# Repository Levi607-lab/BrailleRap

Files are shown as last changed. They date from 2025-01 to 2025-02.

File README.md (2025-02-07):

<figure> 
 
 # BrailleRAP
 This fork is based on the BrailleRap project: [https://github.com/braillerap/BrailleRap](https://github.com/braillerap/BrailleRap).

After building three BrailleRap machines in the OpenLab at Helmuth Schmidt University, this repository aims to contribute to this fantastic project by:  
- Adding a complete Bill of Materials (BOM) with all necessary screws.  
- Providing a remodeled STL file for the electromagnet guide, designed to fit 4.6 mm spacers.  
- Including pre-configured Marlin firmware for the BrailleRap machine, which only needs to be flashed to the control board using Visual Studio Code.

### Findings
- **Spacer Issue:** The spacers listed in the BOM are too long. The solenoid hits the heatsinks of the stepper motor drivers. To address this, we used self-locking nuts and M3 screws to create custom spacers for the controller board. This solution worked well.  
- **Stylus Punch Calibration:** After calibrating the height of the stylus punch, we applied Loctite to the part of the solenoid that screws into the spacer and the stylus. This prevents the parts from coming loose.  
  - We neglected to do this initially, which caused the machine to become unstable and ultimately damaged one of the stepper drivers.
:)
---

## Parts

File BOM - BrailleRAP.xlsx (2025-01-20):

BOM for BrailleRap for procurement on the German market
outstanding
complete
discrepancies
Bestellung |  |  |  |  |  |  |  |  | Warenannahme
Nr. | Product | Intended use | Quantity | Price (single) | Price (total) | Link | Order date | Delivery date | delivered quantity | received on
1 | 330mm linear shaft d8mm | Brailrap | 2 | 13.74 € | 27.48 € | KGTCN 2 Stück 330mm Länge Linearwelle Gerade Runde Stange Ø8mm Kugellagerstahl Zylinderschiene für 3D Drucker CNC : Amazon.de: Gewerbe, Industrie & Wissenschaft (https://www.amazon.de/KGTCN-Linearwelle-Kugellagerstahl-Zylinderschiene-Drucker/dp/B0CY7TR9RG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)
2 | 100mm linear shaft d8mm | Brailrap | 1 | 7.99 € | 7.99 € | 2Pcs 8mm x 100mm Linearwelle Gerade Rundstange 8mm Durchmesser Linearführung Horizontale Präzisionswelle Linearlager für 3D Drucker CNC : Amazon.de: Gewerbe, Industrie & Wissenschaft (https://www.amazon.de/Linearwelle-Durchmesser-Linearf%C3%BChrung-Horizontale-Pr%C3%A4zisionswelle/dp/B08XYMPX9S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)
3 | 400mm Linear shaft d8mm (actually 365) | Brailrap | 1 | 14.99 € | 14.99 € | 2Pcs 8mm x 400mm Linearwelle Gerade Rundstange 8mm Durchmesser Linearführung Horizontale Präzisionswelle Linearlager für 3D Drucker CNC : Amazon.de: Gewerbe, Industrie & Wissenschaft (https://www.amazon.de/Linearwelle-Durchmesser-Linearf%C3%BChrung-Horizontale-Pr%C3%A4zisionswelle/dp/B08XYN6DDC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)
4 | Plain bearing rJ4PJp | Brailrap | 1 | 14.98 € | 14.98 € | 3D FREUNDE 12x Original Igus RJ4JP-01-08 Gleitlager Upgrade für LM8UU Lager für 3D Drucker RepRap Mendel Anet A8 A6 Makerbot mk8 Creality Flashforge : Amazon.de: Gewerbe, Industrie & Wissenschaft (https://www.amazon.de/Original-Igus-RJ4JP-01-08-Gleitlager-Flashforge/dp/B079P717LJ?adgrpid=1192970771146211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)
5 | GT2 pulley 20 teeth 8mm bore | Brailrap | 1 | 6.99 € | 6.99 € | WINSINN GT2 Riemenscheibe, 20 Zähne, 8 mm Bohrung, 6 mm Breite, 20 Zähne, Zahnriemenscheibe, Rad, Aluminium, für 3D-Drucker (5 Stück) : Amazon.de: Gewerbe, Industrie & Wissenschaft (https://www.amazon.de/Aluminium-20-Z%C3%A4hne-Zahnriemenscheibe-Zahnriemen-i3-Kossel/dp/B077GMKW1C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)
6 | GT2 pulley 20 teeth 3mm bore | Brailrap | 2 | 6.49 € | 12.98 € | GT2 Umlenkrolle, Pulleye, 20 Zähne 3mm M3 Bohrung für 6mm Zahnriemen mit hochwertigem Lager, 2GT, z. B. BLV Cube : Amazon.de: Gewerbe, Industrie & Wissenschaft (https://www.amazon.de/Umlenkrolle-Pulleye-Bohrung-Zahnriemen-hochwertigem/dp/B09256JK7B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)
7 | GT2 pulley 20 teeth 5 mm bore | Brailrap | 1 | 6.99 € | 6.99 € | Winsinn GT2 Riemenscheibe, 20 Zähne, 5 mm Bohrung, 6 mm Breite, 20 Zähne, Zahnriemenscheibe aus Aluminium für 3D-Drucker (5 Stück) : Amazon.de: Gewerbe, Industrie & Wissenschaft (https://www.amazon.de/Aluminium-20-Z%C3%A4hne-Zahnriemenscheibe-Zahnriemen-i3-Kossel/dp/B077GNZK3J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)
8 | KP08 Bearing mounting block 8mm bore | Brailrap | 1 | 9.99 € | 9.99 € | Saipor 4 Stück KP08 Lager Montageblock 8mm Bohrung Zinklegierung Einsatzkugellager Lagersitz Gussgehaeuse Lager Stehlager Lagerbock 3D-Druckerzubehör-Kit : Amazon.de: Gewerbe, Industrie & Wissenschaft (https://www.amazon.de/Saipor-Montageblock-Zinklegierung-Einsatzkugellager-3D-Druckerzubeh%C3%B6r-Kit/dp/B08X6Q6194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)
9 | KFL08 vertical ball bearing 8mm bore | Brailrap | 1 | 6.99 € | 6.99 € | QWORK® 6 Stück KFL08 Flanschlager, Stehlager 8mm, Zinklegierung Innenkugel, Stehlagereinheit Kugellager für 3D Drucker : Amazon.de: Gewerbe, Industrie & Wissenschaft (https://www.amazon.de/QWORK-Flanschlager-Zinklegierung-Innenkugel-Stehlagereinheit/dp/B0BBTYYJ9J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)
10 | Flex coupling 5 to 8 mm shaft | Brailrap | 1 | 10.99 € | 10.99 € | https://www.amazon.de/Flexible-Aluminiumgeh%C3%A4use-Sechskantschl%C3%BCssel-3D-Drucker-CNC-Maschine/dp/B09XK4T8D2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
11 | Closed GT2 6mm belt | Brailrap | 1 | 8.49 € | 8.49 € | Turmberg3D GT2 geschlossener Zahnriemen - 6mm breit - Länge 200mm - je 2 Stück - Zugstrang aus Glasfaser (200mm) : Amazon.de: Gewerbe, Industrie & Wissenschaft (https://www.amazon.de/geschlossener-Zahnriemen-breit-St%C3%BCck-200mm/dp/B07D92S592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)
12 | GT2 6mm belt 10 m | Brailrap | 1 | 11.99 € | 11.99 € | GT2 riemen 6mm x 10M für 3D Drucker GT2 riemen 6mm : Amazon.de: Gewerbe, Industrie & Wissenschaft (https://www.amazon.de/GT2-riemen-6mm-10M-Drucker/dp/B097QPRGCJ?__mk_de_DE=%C3%85M%C3%85%C5%BD%C3%95%C3%91)
13 | O-ring 15.1 x 20.5 x 2.7 mm | Brailrap | 3 | 3.19 € | 9.57 € | https://www.dkl-kugellager-shop.de/O-Ring-VITON-151x27-FPM75-R12-BLACK
14 | GT2 torsion spring | Brailrap | 1 | 4.99 € | 4.99 € | S SIENOC Silber Metall GT2 Zahnriemenspanner Torsionsfeder für 3D-Drucker RepRap 6mm Breite Gürtel Packung mit 10 : Amazon.de: Gewerbe, Industrie & Wissenschaft (https://www.amazon.de/SIENOC-Zahnriemenspanner-Torsionsfeder-3D-Drucker-Packung/dp/B01MYUY5MT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)
15 | Stepper motor driver | Brailrap | 1 | 17.99 € | 17.99 € | AZDelivery 5 x DRV8825 Schrittmotor-Treiber-Modul mit Kühlkörper, z.B. für RAMPS 1.4, CNC-Shield, 3D Drucker, Prusa Mendel kompatibel mit Arduino und Raspberry Pi inklusive E-Book! : Amazon.de: Gewerbe, Industrie & Wissenschaft (https://www.amazon.de/AZDelivery-DRV8825-Schrittmotor-Treiber-Modul-K%C3%BChlk%C3%B6rper-CNC-Shield/dp/B07YWV6W4W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)
16 | Motherboard MKS GEN -L 2.1 | Brailrap | 1 | 35.45 € | 35.45 € | Yklhsocneg 3D Drucker Motherboard MKS GEN-L V2.1 Steuerplatine Motherboard Kompatibel mit : Amazon.de: Gewerbe, Industrie & Wissenschaft (https://www.amazon.de/Yklhsocneg-Drucker-Motherboard-Steuerplatine-Kompatibel/dp/B0CGTXXJ5R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)
17 | Power supply 12 V 72 W | Brailrap | 1 | 10.99 € | 10.99 € | Sporgo 72W Netzteil 12V 6A LED Trafo: Universal AC DC Netzteil Transformator Spannungswandler 230v auf 12 Volt für 3528/5050 LED Streifen CCTV Kamera, 12V Adapter Schalttransformatoren 72 Watt max: Amazon.de: Baumarkt (https://www.amazon.de/Sporgo-Netzteil-Trafo-Spannungswandler-Schalttransformatoren-Schwarz/dp/B0BZYWS63C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)
18 | Diodes | Brailrap | 1 | 5.99 € | 5.99 € | ALLECIN 150 Stück 1N4004 Gleichrichter Diode 1A 400V IN4004 4004 Axial 1Amp 400Volt Gleichrichterdiode Rectifier Dioden DO-41 : Amazon.de: Gewerbe, Industrie & Wissenschaft (https://www.amazon.de/ALLECIN-1N4004-Gleichrichter-Gleichrichterdiode-Rectifier/dp/B0CKRKYZ9B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)
19 | Power Jack DC socket | Brailrap | 1 | 7.99 € | 7.99 € | CLDIY 2.5mm DC Power Jack Buchse, Panelmontage DC Power Jack Buchse Panelmontage Anschluss 20St : Amazon.de: Elektronik & Foto (https://www.amazon.de/Clyxgs-2-5mm-Buchse-Panelmontage-Anschluss/dp/B081CM1G4M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)
20 | 0826B Solenoid Solenoid | Brailrap | 1 | 12.29 € | 12.29 € | https://www.amazon.com/0826B-Frame-Solenoid-Electromagnet-Stroke/dp/B07P2ST2VF
21 | Nema 17 17HS4401 | Brailrap | 1 | 26.99 € | 26.99 € | Twotrees Nema 17 Moteur couple élevé 1.5A (17HS4401) 42N.cm (60 oz.in) 1.8 degrés 38MM 4 fils avec câble 1m et connecteur pour imprimante 3D93 (3 Pack) : Amazon.de: Gewerbe, Industrie & Wissenschaft (https://www.amazon.de/Twotrees-Moteur-17HS4401-connecteur-imprimante/dp/B07STT1876)
22 | Grub screw m3 x 16 mm with pin | Brailrap | 1 | 2.19 € | 2.19 € | https://www.amazon.de/Gewindestifte-mit-Innensechskant-Zapfen-Madenschrauben/dp/B06XBS3K73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
23 | M3 cylinder head screws | Brailrap | 1 | 13.99 € | 13.99 € | https://www.amazon.de/Faankiton-600-Zylinderschrauben-Sechskantschrauben-Kohlenstoffstahl/dp/B0CFY6V3HV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
24 | m3 x cylinder head screws | Brailrap | 1 | 3.99 € | 3.99 € | meinschraubenversand.de - Zylinderschrauben M3x14 10 Stück DIN 912 (Teilgewinde, Zylinderkopfschrauben, Innensechskant, ISO 4762) A2 V2A rostfreier Edelstahl - M3 x 14 : Amazon.de: Baumarkt (https://www.amazon.de/meinschraubenversand-Zylinderschrauben-Zylinderkopfschrauben-Inbusschrauben-Innensechskant/dp/B0BNJXRWG3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)
25 | Limit switch | Brailrap | 1 | 8.99 € | 8.99 € | Taiss/10 stücke 250V 5A 2Pin Taktschalter Empfindliche Mikroschalter Mikroschalter Griff Endschalter KW11-3Z-02 : Amazon.de: Baumarkt (https://www.amazon.de/dp/B07GLK29JR?s=industrial&sp_csd=d2lkZ2V0TmFtZT1zcF9kZXRhaWw)
26 | Washers wide | Brailrap | 1 | 5.89 € | 5.89 € | https://www.amazon.de/Unterlegscheiben-Edelstahl-Karosseriescheiben-rostfreie-Gewindestangen/dp/B0C36ZMMCG
27 | Washers medium | Brailrap | 1 | 5.59 € | 5.59 € | Flach Unterlegscheiben,100 Stück M3 Edelstahl Flach Unterlegscheiben Beilagscheiben Sortiment Set : Amazon.de: Baumarkt (https://www.amazon.de/Unterlegscheibe-Sortiment-Unterlegscheiben-metrischer-best%C3%A4ndig/dp/B08D7R14C9)
28 | M5 self-locking nuts | Brailrap | 1 | 4.99 € | 4.99 € | Selbstsichernde Muttern M5 DIN 985 Sicherungsmuttern Edelstahl A2 V2A Stopmuttern Sechskantmuttern (50 Stück) : Amazon.de: Baumarkt (https://www.amazon.de/Selbstsichernde-Sicherungsmuttern-Edelstahl-Stopmuttern-Sechskantmuttern/dp/B0CC5R7NCL)
29 | M3x30 grub screws | Brailrap | 1 | 6.99 € | 6.99 € | https://www.amazon.de/dp/B07TZJCCH4/ref=twister_B07TZJDTSV?_encoding=UTF8&th=1
30 | M3 self-locking nuts | Brailrap | 1 | 3.99 € | 3.99 € | https://www.amazon.de/140-Selbstsichernde-Sechskantmuttern-Sicherungsmuttern-Kontermuttern/dp/B0D1V6WKQP
31 | M5 x 18 cylinder head screw | Brailrap | 1 | 2.22 € | 2.22 € | Zylinderschrauben mit Innensechskant - M5x18 - (10 Stück) - DIN 912 (ISO 4762) - Vollgewinde - Zylinderkopfschrauben - aus rostfreiem Edelstahl A2 V2A - SC912 : Amazon.de: Baumarkt (https://www.amazon.de/Zylinderschrauben-mit-Innensechskant-Vollgewinde-Zylinderkopfschrauben/dp/B01H9HG6I6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)
32 | M5 x 25 Cylinder head screw | Brailrap | 1 | 2.39 € | 2.39 € | https://www.amazon.de/Zylinderschrauben-mit-Innensechskant-Vollgewinde-Zylinderkopfschrauben/dp/B01H9HGC4E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
33 | M3x 6 grub screw | Brailrap | 1 | 9.10 € | 9.10 € | Techtanium® Gewindestifte M3 x 6 mm mit Innensechskant u. Kegelkuppe aus Edelstahl A2 (5 Stück) | Versch. Größen & Verpackungseinheiten verfügbar | Madenschrauben | Schraubstifte | DIN 913 : Amazon.de: Baumarkt (https://www.amazon.de/Techtanium%C2%AE-Gewindestifte-Innensechskant-Madenschrauben-Schraubstifte/dp/B0CC9J2RR6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)
34 | M3 x 12 grub screw | Brailrap | 1 | 5.84 € | 5.84 € | Madenschrauben Niro M3 x 12/50 Stück Edelstahl A2 / V2A (AISI 304) DIN 913 Gewindestifte : Amazon.de: Baumarkt (https://www.amazon.de/dp/B07L6C6SKF/ref=twister_B07L69RGV7?_encoding=UTF8&th=1)
35 | M5 washers | Brailrap | 1 | 5.13 € | 5.13 € | Unterlegscheiben M5 Verzinkt Stahl - DIN 9021 - Beilagscheiben - U-Scheiben - Flache Unterlegscheiben (Große: M5; Menge: 25 St.) : Amazon.de: Baumarkt (https://www.amazon.de/Unterlegscheiben-Verzinkt-Stahl-Beilagscheiben-U-Scheiben/dp/B0CK2PLRKP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)
36 | Spacer | Brailrap | 1 | 13.08 € | 13.08 € | CONPHERON Weiblich Messing-Säulen Abstandshalter Distanzhülse Weiblich Gewinde Abstandsbolzen M3*20 mm,20 Stück : Amazon.de: Baumarkt (https://www.amazon.de/CONPHERON-Messing-S%C3%A4ulen-Abstandshalter-Distanzh%C3%BClse-Abstandsbolzen/dp/B09NZSB5JN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)
37 | M2.5 x 14 | Brailrap | 1 | 3.72 € | 3.72 € | Zylinderschrauben mit Innensechskant - M2,5x14 - (25 Stück) - DIN 912 (ISO 4762) - Vollgewinde - Zylinderkopfschrauben - aus rostfreiem Edelstahl A2 V2A - SC912 : Amazon.de: Baumarkt (https://www.amazon.de/Zylinderschrauben-mit-Innensechskant-Vollgewinde-Zylinderkopfschrauben/dp/B01IMFRTK8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)
38 | ABS+ | Brailrap | 1 | 17.99 € | 17.99 € | eSUN ABS+ Black - 3DJake Deutschland (https://www.3djake.de/esun/abs-black-6)
39 | M2.5 nut | Brailrap | 1 | 0.75 € | 0.75 € | https://www.amazon.de/DIN-934-Sechskantmutter-Edelstahl-St%C3%BCck/dp/B08VQ9SHLW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
40 | 2600mm x 400mm x 5mm plywood sheets | Brailrap | 1 | 0.75 € | 0.75 € | https://www.amazon.de/DIN-934-Sechskantmutter-Edelstahl-St%C3%BCck/dp/B08VQ9SHLW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
 |  |  |  | Total | 390.68 €

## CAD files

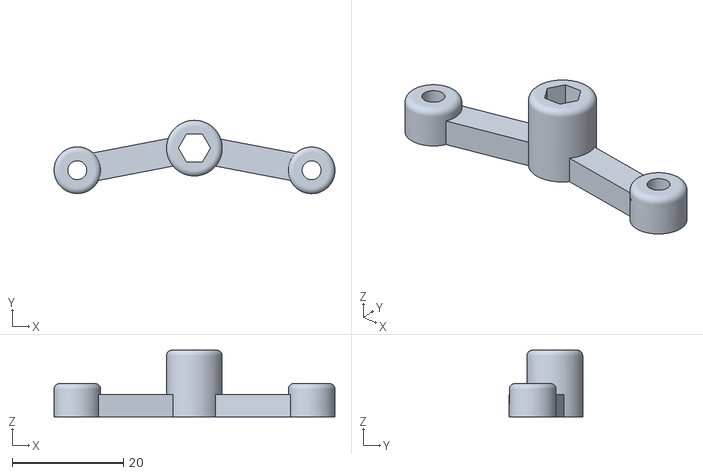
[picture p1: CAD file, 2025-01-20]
printed_parts/ELECTRO_MAGNET_guide_fit 4.6mm (0.2 mm tolerance).stl
50.5 x 13.2 x 12.0
